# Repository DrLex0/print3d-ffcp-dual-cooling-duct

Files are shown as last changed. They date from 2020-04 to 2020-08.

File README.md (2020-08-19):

# FlashForge Creator Pro front dual fan duct
*Cooling duct for both extruders of the FlashForge Creator Pro and similar 3D printers (formerly thing:1675208)*

### License
[Creative Commons - Attribution](https://creativecommons.org/licenses/by/4.0/)

### Gallery

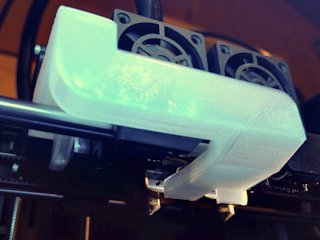
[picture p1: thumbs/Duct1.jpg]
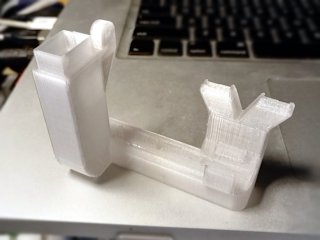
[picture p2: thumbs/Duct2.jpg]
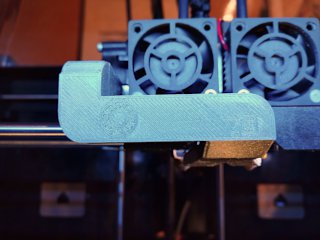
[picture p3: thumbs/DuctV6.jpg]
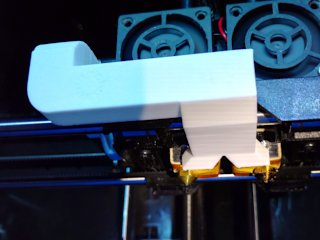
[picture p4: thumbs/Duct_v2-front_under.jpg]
Photo 4 - older prototype
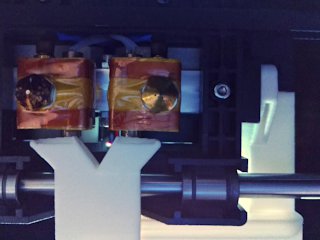
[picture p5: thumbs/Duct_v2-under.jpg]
Photo 5 - underside
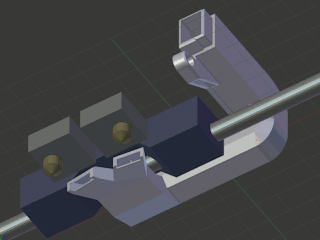
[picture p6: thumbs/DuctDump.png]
Mounting
[🔎](images/Duct1.jpg) [🔎](images/Duct2.jpg) [🔎](images/DuctV6.jpg) [🔎](images/Duct_v2-front_under.jpg) [🔎](images/Duct_v2-under.jpg) [🔎](images/DuctDump.png)

## Description and Instructions

This is a drop-in replacement fan duct that fits the *FlashForge Creator Pro* and similar models that have the ‘turbo fan’ at the left of the nozzles. It has been confirmed to fit the 2015 FFCP (upwards opening door), the 2016 (sideways door), and the Dreamer. It probably also fits clones like CTC and PowerSpec.

The stock duct has an obvious problem: it only cools the left nozzle. This means it pretty much obliges you to always print filaments like PLA with the left nozzle because they require active cooling for a good result. This new duct offers cooling for both nozzles at the same time, which allows to use any filament with any of the nozzles and also do dual extrusions with proper cooling as well.

After reports that the v4 and v5 versions of this duct did not perform as well as the stock duct (for single extrusion with the left nozzle obviously), I made some more improvements and did some extensive tests that confirmed the new v6 outperforms the stock duct on a particular challenging model. It is possible that the stock duct will still provide better results in specific situations, but those should be rare.

If you're only going to print with a single extruder, check out [the single-extruder variation of this duct](https://github.com/DrLex0/print3D-ffcp-left-cooling-duct), it provides even better cooling.
 

### Pre-printing: check nozzle height

There are two models to choose from. To determine which one you need, do the following test. *Move the bed against the nozzles (as if you are going to use the levelling sheet), then bring the carriage forward and measure the distance between the bed surface and the cradle as shown in the photo.*

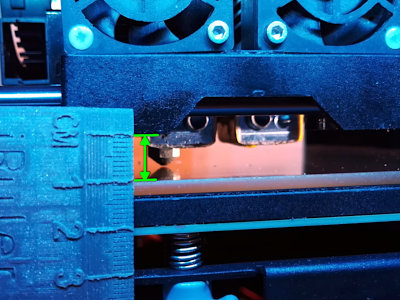
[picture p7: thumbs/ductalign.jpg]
Alignment
[🔎](images/ductalign.jpg)

The regular duct model is designed to be optimal if this distance is **10 mm,** which is normally the case on a standard FFCP. It should also be this way if you aligned the nozzles with [this leveler](https://www.thingiverse.com/thing:1582720).

The ‘x1’ model is for when this distance is **11 mm.** This is likely the case if you installed Micro Swiss all-metal hot-ends and followed their instructions exactly.

If your nozzles are at a considerably different height, you should consider realigning them. If that's not possible, your only option is to modify the duct model.
 

### Printing

**Do not print this in PLA:** it is likely to deform from the heat of the nozzles and possibly the heated bed as well. The duct must be printed in a filament that can withstand a good amount of heat. PETG is not recommended either: it will deform as I found out by experience. Polycarbonate would be ideal, but is of course more difficult to print. You *might* get away with PLA or PETG if you apply heat insulation as described below, but still I wouldn't recommend this.

**ABS** is generally the most suitable material for this, because it is pretty resistant against heat and it is not terribly difficult to print it on a FFCP.

Make sure to **disable supports,** otherwise the duct may be blocked by material added on the inside. You could use soluble supports, but the model is designed to be printed easily without supports, and a raft or brim should also be unnecessary. Just ensure your bed is well-levelled and you have no problems printing bridges. The model has internal structures to minimise the risk of problems caused by your slicer and printer, but only if you print it with the intake pointing upwards.

I printed this in Slic3r with 0.2 mm layers, 100% infill, *no* supports and no raft. I used two perimeters, 2 top layers and 2 bottom layers. Do not try to skimp on infill: the model consists almost entirely of thin walls anyway. 100% is needed to ensure strength of the few small solid parts. You won't be saving much filament or weight by trying to enforce a lower infill, it would only make the duct weaker.

Do not rush this print. To get a strong result, print *slowly* and only provide the minimum amount of cooling necessary. If you can control fan speed (which is **not** the case on an unmodified FFCP), you can enable it all the time on an ABS print at about 10% to 20%. Otherwise, only enable the fan while overhangs are being printed. You should get an OK result without fan altogether.

Printing in a translucent material has the advantage that it will pass through some of the light from the LED strip, but it is advisable anyhow to add [an extra LED](https://github.com/DrLex0/print3d-ffcp-x-led-mount) to get a better view on what is being printed.
 

### Post-printing

The only essential post-processing step is to ream the small hole next to the screw with a 2mm drill, this will ensure a perfect and snug fit.

The tips of the exhausts are very close to the heater blocks, which can cause deformation over time. This should not be too much of a problem if you only print PLA at relatively low temperatures, especially considering that the fan should be always on for PLA hence the duct will keep itself cooled. When printing ABS or PETG however, or other filaments that require a high extrusion temperature with little cooling, the duct is likely to deform, even if it was printed in ABS.
The most effective way to mitigate this, is to cover the tips of the exhausts in a layer of insulating material. What works really well is one layer of self-adhesive aluminium foil with a layer of kapton on top, as shown in the photo below. A few layers of foil or kapton alone however will probably be effective as well.

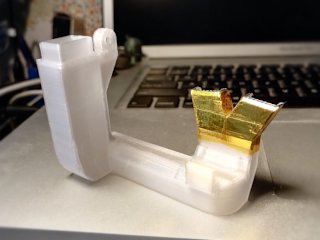
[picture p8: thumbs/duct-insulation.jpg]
Insulation
[🔎](images/duct-insulation.jpg)

*Insulating the duct like this will ensure it won't deform even when printing at high temperatures.*

You can also add some extra heat insulation to your hot-end heater blocks (especially the front). This helps to avoid that the blocks lose heat when air from the exhausts is reflected against the bed during the lower part of the print. A few layers of kapton tape might be sufficient, but an extra layer of true insulation material will be more effective. I found some insulation on eBay that I could cut into strips, and by making a hole with a perforator, I can push-fit the insulation onto the round element in the heater block, which makes it easy to remove.
 

### Installing

Mounting is very easy. You will have a tiny bit of margin to wiggle the duct up and down, ensure it is not rubbing against the rail by pushing it down while tightening the screw. The little tab should be resting on top of the cradle. I recommend to glue a thin piece of rubber (or flexible filament) onto the carriage under the tab, such that the duct won't rattle due to vibrations.

Even though it is considerably larger than the stock fan duct, my ABS print of the v5 duct weighs exactly the same as the stock duct so there should be no impact on print performance.

If you want to retrofit the blower fan and this duct on an older printer that does not have the mounting bracket, you can print [my clone of it](https://www.thingiverse.com/thing:2086927).
 

### Using

Just as with the stock duct, a limitation is that it only blows in one direction, meaning that parts in the ‘shadow’ of the nozzle (i.e. at the back) will get the least cooling. If possible, orient the model such that overhangs or whatever parts should look best, are at the front. Again, if you will only be printing with one extruder, the [single-extrusion variation of this duct](https://github.com/DrLex0/print3D-ffcp-left-cooling-duct) reduces the shadow problem.

If you're going to do a long print where the fan is not needed, you should remove the duct altogether. This is especially the case with filaments like polycarbonate that need to be printed at very high temperatures. When no air is flowing through the duct, the long exposure to the heat of the extruders is very likely to cause the exhausts to deform, even if printed in ABS and even if you applied extra insulation.

You can enable the fan on ABS prints to improve quality, but this will greatly increase the risk of warping and cracking. Enabling the fan continuously with ABS is only feasible in the following cases:
* for small objects printed with thin layers. Be sure to increase your print temperature if you do, and seal the enclosure to keep the air inside cozy and warm. A raft can also help to prevent warping.
* for large objects when using the smart cooling features of your slicer software to only enable the fan during short periods while printing overhangs.
* if you can drastically reduce the speed of the fan. Don't bother trying to vary the speed in your slicer program, the fan circuit in the FFCP is on/off only. The simplest way to obtain variable fan speed is by installing a hardware [PWM controller](https://www.thingiverse.com/thing:2095862). There are also some custom Sailfish firmware builds that have a software PWM implementation, but it is limited. A more complicated but also fully automatic solution is [this one](https://github.com/DrLex0/MightyVariableFan), where fan speed is delegated to a separate controller steered by commands in the print code itself.

Similar remarks hold for PETG: it is very sensitive to cooling but you will obtain nicer prints when applying just a tiny bit of cooling, which is only possible by controlling fan speed.
 

If you really like this and want to show appreciation for the work I've put into this, [a small tip is always welcome](https://www.dr-lex.be/about/#contact).
 

## How I Designed This

### The basics

The screw mounting part was taken from [FFCP DUCT by natewin](https://www.thingiverse.com/thing:1469817), for the rest this was designed from scratch.

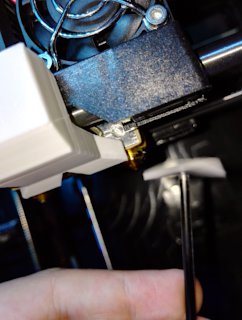
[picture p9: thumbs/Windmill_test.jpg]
Windmill
[🔎](images/Windmill_test.jpg)

*The ‘windmill test’*

I created the first iteration by measuring the dimensions of the FFCP printing assembly with a caliper, and making a rough model of it in Blender. Then I constructed the duct around this model. For the exhaust shapes I started out with a wet-finger guess. This seemed to do the job at first but eventually I noticed it didn't perform well. To find out in what direction the air really was being blown, I printed a small windmill that can be mounted on an empty ballpoint refill, and enabled the fan with a custom x3g file. This showed the air was aimed way too much downward, and also at a wrong angle in the horizontal plane. So I tweaked the exhaust shapes and printed new ones, testing them with the little windmill until the airflow was just right. Of course I didn't re-print the entire duct every time, only the exhaust part which I attached to the decapitated duct with some adhesive tape (nope, not with *duct* tape, just ordinary tape).

I did the same windmill test on the stock fan duct and it suffers from a poorly aimed airflow. So even if you will never print with more than one nozzle, this should still be a noticeable upgrade.

### The refinements

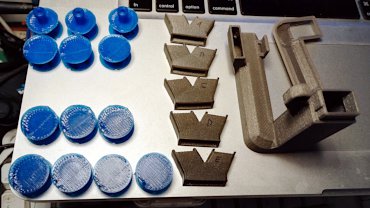
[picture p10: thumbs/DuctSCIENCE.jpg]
Now with more science!
[🔎](images/DuctSCIENCE.jpg)

For the v6 version, I went even further and compared the performance of new prototypes to the stock duct and the v5. For this, I created a small [mushroom-shaped model](http://www.thingiverse.com/thing:2005832) which I printed in PLA at a higher temperature than usual. This model warps like crazy without proper cooling. Because my duct blows from the front unlike the stock duct which blows from the left, I manipulated the test GCode file by rotating all coordinates 90° clockwise to make the comparison as fair as possible. This ensured that when printing the test with the stock duct, exactly the same movements were made with the air blowing roughly from the same direction w.r.t. the orientation of the model.
 

## Updates

### Version 1 (July 16, 2016)
First release.

### Version 2 (July 27, 2016)
If you printed the first version, you will definitely want to upgrade to this one: the first version directed its air way too much downwards and performed even worse than the stock duct (which also doesn't really produce any appreciable airflow at the height of the nozzle). This new duct should allow to print overhangs that previously ended in disaster, with *both* nozzles. Moreover, it requires less material, making it lighter than the first one.

### Version 3 (October 1, 2016)
This is a minor upgrade from v2, the only differences are that it has thinner walls and other tweaks to require less material, and I modified the bottom to reduce obstruction of the view. I specifically made this version to be printed in PETG. Even though PETG is considerably heavier than ABS, thanks to the weight trimming v3 weighs less in PETG than v2 did in ABS. However, my PETG duct eventually started to melt so I do not recommend it, unless you always enable the fan and print at low temperatures.

### Version 4 (October 15, 2016)
Again small changes, most important is that the exhausts are slightly further away from the heaters, this provides a better directed airflow and lower risk of melting. Also some more weight trimming.

### Version 5 (December 18, 2016)
Added plugs, rounded one of the corners mainly for aesthetic reasons (although it could help a bit to reduce turbulence), also improved airflow where the exhaust joins the main body. Again shaved off a bit of material as well, and tweaked some of the internal structures to reduce the risk that slicer programs will make a mess out of the ‘ceiling’ part.
(Small update December 20th: chamfered the inlet as per suggestion by user FlashErase, to make it easier to install the duct.)

### Version 6 (December 30, 2016)
Increased the radius of the front right corner (this really should reduce turbulence), and made other small airflow improvements. Redesigned the exhausts to be larger and better directed, and incorporated small baffles to ensure the air is aimed directly at the nozzles. Also incorporated small details that increase the chance of good bridging. Small bonus: it produces a slight jet engine sound.

Removed the v2 model: the v6 should be so easy to print and is so much better than the v2, that there is no point anymore in allowing people to print this old version. Dropped the plugs as well: they were way too finicky to install and remove, and they caused the fan to spin faster, which could cause it to wear out quickly.

### Version 6r (May 7 and Dec 19, 2017)
No functional differences with v6, only some reinforcements have been added around the region where the duct is the weakest. If you have already printed the v6 and do not have problems with it, then there is no reason to print this one.

Dec 19: added the ‘x1’ variation, which has the exhausts 1 mm lower than the normal duct, in case your nozzles are 1 mm lower than the stock nozzles (e.g. you installed all-metal hot-ends).

### Version 6s (Apr 25, 2020)
Even fewer changes, there is absolutely no need to re-print this if you already have v6r. The only change, besides leaving the sinking ship of Thingiverse, is that I removed the tiny bit that was still a copy of natewin's model, and made it again from scratch. (I found it a bit ridiculous to have to label this as a remix just because of that tiny shared part.)

### Future plans
When I find the time, I will run this duct through the same kind of CFD simulations as I have done with the [single-extruder variation](https://github.com/DrLex0/print3D-ffcp-left-cooling-duct), to ensure the flows are as optimal as possible within the limitations of this design.

## Tags

`baffle`, `cooling`, `cooling_duct`, `dual_extrusion`, `fan_duct`, `FFCP`, `FFCPRo`, `FlashForge_Dreamer`, `upgrade`

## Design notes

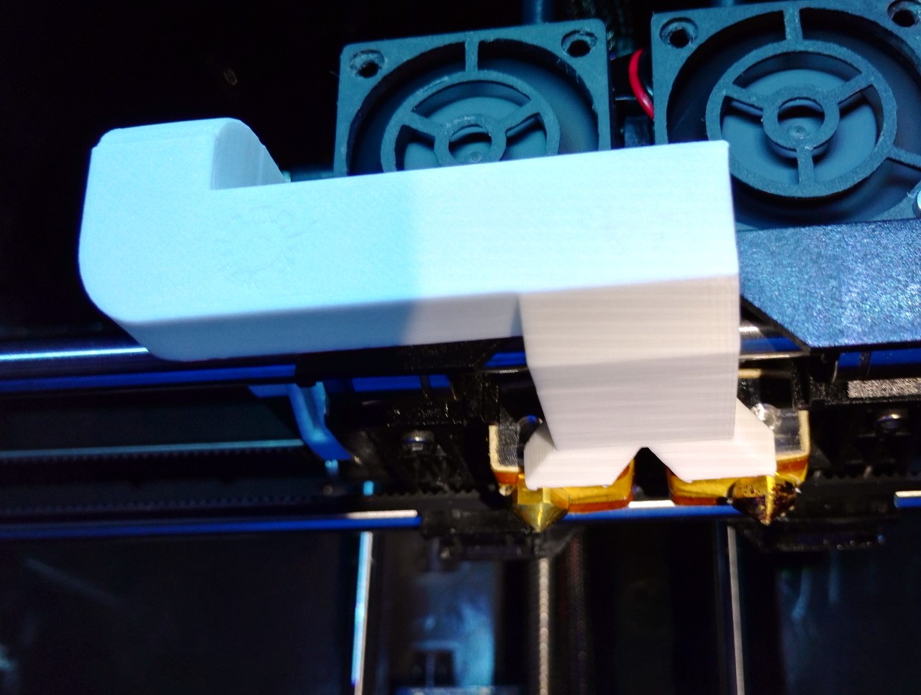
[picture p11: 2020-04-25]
images/Duct_v2-front_under.jpg

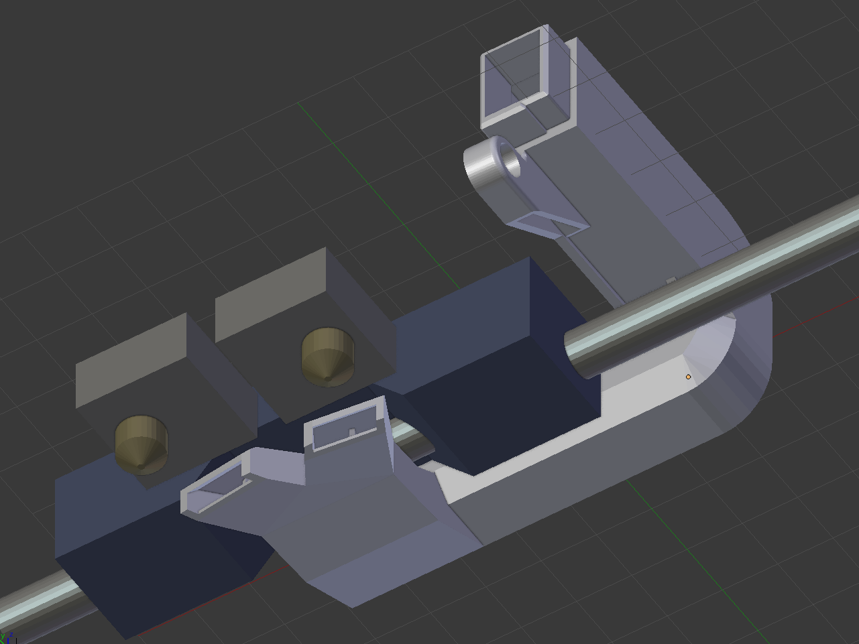
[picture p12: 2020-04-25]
images/DuctDump.png

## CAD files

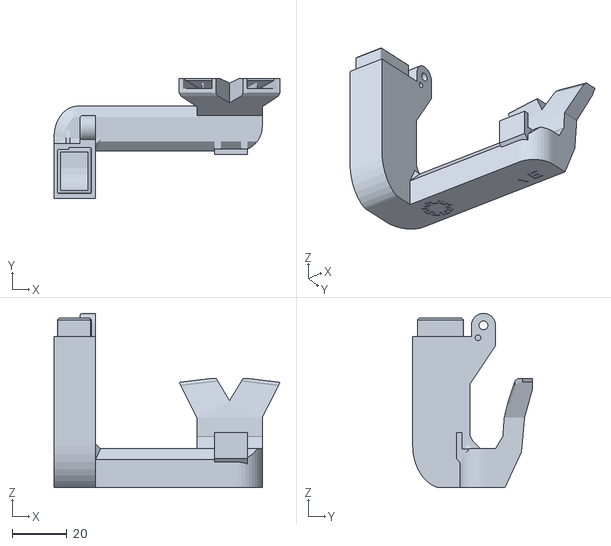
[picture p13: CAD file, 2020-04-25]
FF_Creator_Pro-front_dual_duct_v6s.stl
82.5 x 43.7 x 63.6

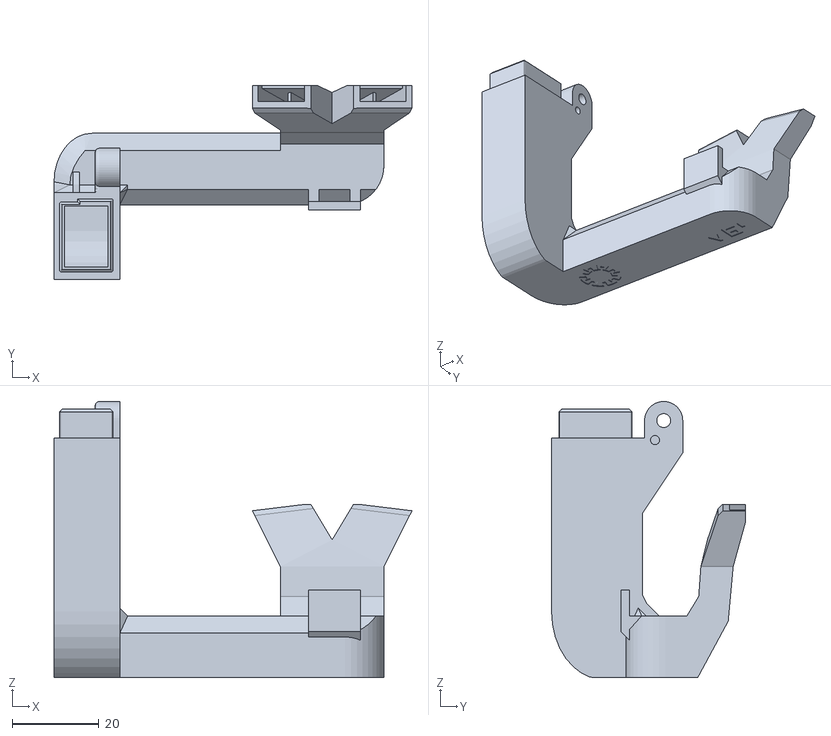
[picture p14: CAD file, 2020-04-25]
FF_Creator_Pro-front_dual_duct_v6s_x1.stl
82.5 x 44.7 x 63.6

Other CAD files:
FFCP-DualDuct.blend

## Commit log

2020-04-25 Thingiverse exodus model 7: migrate to GitHub
    [FFCP-DualDuct.blend, FF_Creator_Pro-front_dual_duct_v6s.stl, FF_Creator_Pro-front_dual_duct_v6s_x1.stl]
2020-08-19 Uniform pre-printing instructions for both duct variations
